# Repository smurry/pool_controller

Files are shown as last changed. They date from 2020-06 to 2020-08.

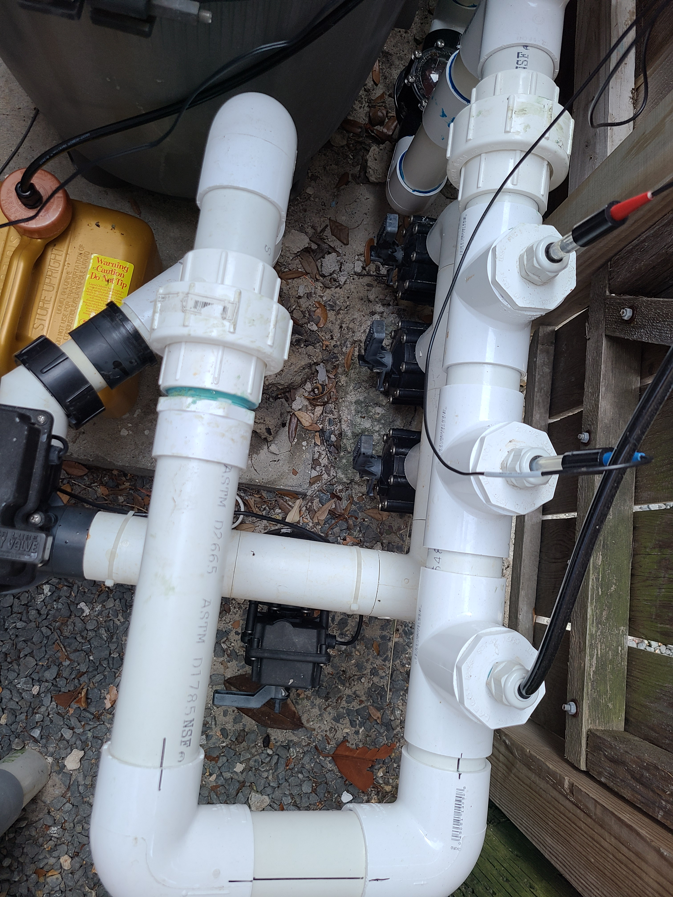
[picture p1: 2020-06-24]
Resources/Sensors and Bleach Canister.jpg

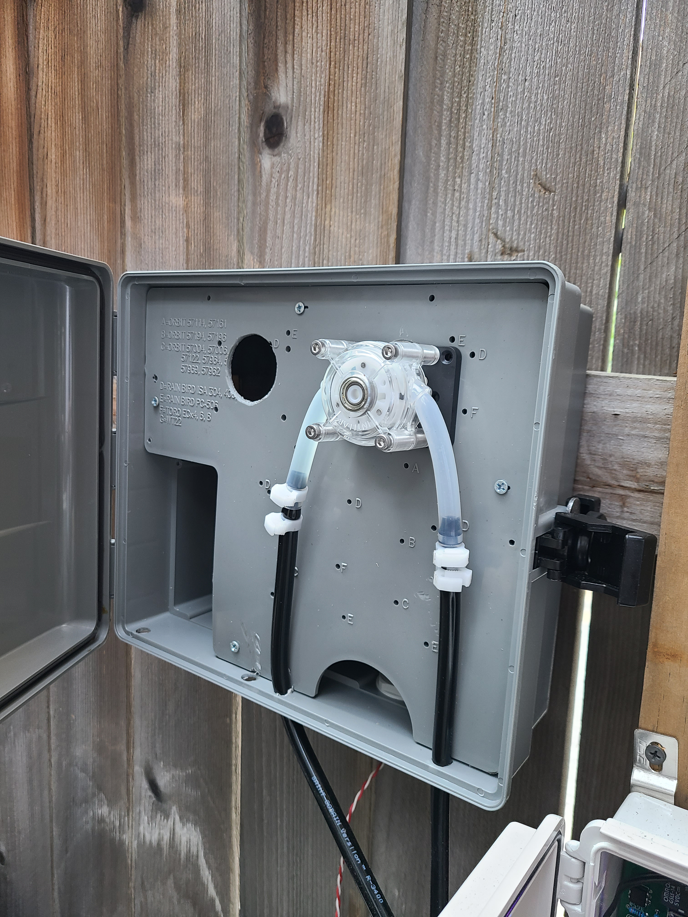
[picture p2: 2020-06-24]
Resources/Bleach Pump.jpg

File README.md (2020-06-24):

# Pool Controller
PH and ORP monitor/control for ESP32

To use, you'll need to flash an ESP32 module with micropython.  See: https://micropython.org/download/esp32/.  Version must be May 20,2020 or later.

You must update the conf-example.sample file:
  1)  edit wifi information and mqtt server information as noted in the file.  All values need to be in quotation marks as in the example file.
  2)  save the file with exactly this filename: conf.txt

After saving the conf.txt file, upload conf.txt, config.py, mqtt_as.py and main.py to the ESP32.  If you are unfamiliar with how to do this, check out https://github.com/BetaRavener/uPyLoader

The sensors configured in the conf.txt file represent IO ports on the ESP32-DEVKITC board.  They are designed to work with isolated carrier boards from Atlas Scientific (for example https://www.atlas-scientific.com/carrier-boards/electrically-isolated-ezo-carrier-board-gen-2/).  You will need to purchase the carrier boards, EZO modules, and probes from Atlas.

Outputs are provided on the IO ports noted in the conf.txt file for Ph Pump (i.e. acid) and ORP Pump (i.e. bleach).  These pins can be connected through appropriate isolation and relays to peristaltic pumps used to dispense the required chemicals into the pool.

This system was designed to work with Home Assistant, although in principle any MQTT-enabled controller should work.  Configuration files for Home Assistant are in the directory "Home Assistant."  The .yaml package goes into your packages directory and the pool_fc.py is an appdaemon file and should go in the appropriate appdaemon folder.

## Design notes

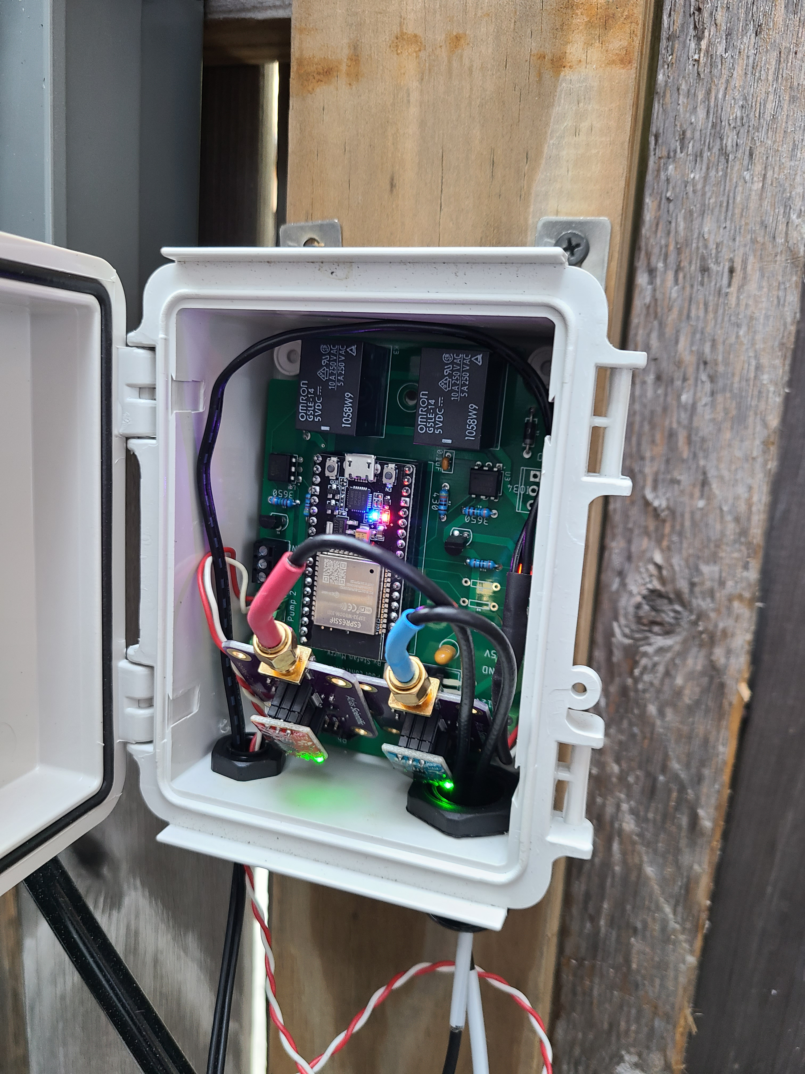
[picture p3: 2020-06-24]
Resources/PH-ORP Controller v2.jpg

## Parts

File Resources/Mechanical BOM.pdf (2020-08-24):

Other parts you’ll need:

Qty | Description | P/N | Website | Notes
6 | Cable Glands | RDC16NA‐GR | https://www.elecdirect.com/cord‐grips‐strain‐relief/cable‐glands/dome‐cap‐cable‐gland‐1‐2‐npt‐39‐ 56‐gray‐complete‐with‐o‐ring‐locknut
2 | Peristaltic Pumps | DP520‐460 | https://www.aliexpress.com/item/32972643254.html?spm=a2g0s.9042311.0.0.55f94c4dxG6wrN
1 | 12VDC Power Supply | N/A | https://www.amazon.com/gp/product/B07H23JGS6/ref=ppx_yo_dt_b_asin_title_o03_s00?ie=UTF8&psc=1
Vari es | 1/4" ID x 3/8" OD x 1/16" Wall Versilon™ R‐3400 UV Resistant Tubing | 33932 | https://www.usplastic.com/catalog/item.aspx?itemid=3 3932 | Sold in 10’ lengths. Need to order as much as needed for your project
4 | .351" Min. to .394" Max. Snap Grip Clamp | 34082 | https://www.usplastic.com/catalog/item.aspx?itemid=3 4082
2 | 1/4" Hose ID x 1/4" Hose ID Black HDPE Connector | 28098 | https://www.usplastic.com/catalog/item.aspx?itemid=2 8098
1 | Outdoor Timer Box | 57095 | https://www.homedepot.com/p/Orbit‐Outdoor‐Timer‐Box‐57095/100158884
1 | Control Board Box | WH‐02 | https://www.polycase.com/wh‐02 | Box matches the board outline and mounting holes

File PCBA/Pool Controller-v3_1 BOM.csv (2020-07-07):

Qty | Value | Device | Package | Parts | Digikey P/N | Price (USD) | Line (USD)
4 |  | Screw Terminal Connector - 2 places | SCREWTERMINAL-3.5MM-2 | J1, J3, J4, J11 | 609-4725-ND | 0.69 | 2.76
2 |  | Screw Terminal Connector - 3 places | SCREWTERMINAL-3.5MM-3 | J6, J12 | ED2741-ND | 0.42 | 0.84
2 |  | Screw Terminal Connector - 4 places | SCREWTERMINAL-3.5MM-4 | J13 | use 2 609-4725-ND | 0.69 | 1.38
1 |  | Switching Regulator-5.5V-TPSM84205EAB | 78XXL | U4 | 296-47074-ND | 5.43 | 5.43
4 | 280 | Axial Resistor-280 ohm | AXIAL-0.3 | R7, R8, R9, R10 | 280XBK-ND | 0.04 | 0.16
1 | 0.1uF | Radial Capacitor - 0.1 uF | CAP-PTH-SMALL-KIT | C1 | 399-9859-1-ND | 0.16 | 0.16
2 | 47uF | Radial Ceramic Capacitor - 47 uF | CPOL-RADIAL-2.5MM-5MM-KIT | C2, C3 | 445-173152-1-ND | 1.09 | 2.18
1 | 10uF | Radial Capacitor - 10 uF | CPOL-RADIAL-2.5MM-5MM-KIT | C4 | 399-3565-ND | 1.50 | 1.50
2 | 1A/50V/1.1V | Radial Diode-1N4001 | DIODE-1N4001 | D1, D2 | 641-1310-1-ND | 0.09 | 0.17
2 | 200mA/40V | NPN Transistor -2N3904 | TO-92 | Q1, Q3 | 2N3904FS-ND | 0.16 | 0.32
2 | 3650 | Axial Resistor-3650 ohm | AXIAL-0.3 | R3, R4 | 3.65KXBK-ND | 0.06 | 0.11
2 | 430 | Axial Resistor-430 ohm | AXIAL-0.3 | R1, R2 | 432XBK-ND | 0.06 | 0.11
1 | 4700 | Axial Resistor-4700 ohm | AXIAL-0.3 | R5 | 4.75KXBK-ND | 0.06 | 0.06
2 | CNY17-1 | Optoisolator - CNY17-1 | DIP762W50P254L730H410Q6 | U2, U3 | 160-1308-5-ND | 0.38 | 0.75
1 | ESP32-DEVKITC-32D | ESP32-DEVKITC-32D | MODULE_ESP32-DEVKITC-32D | U1 | 1965-ESP32-DEVKITC-32UE-ND | 10.00 | 10.00
2 | RELAY-SPDT | Relay - SPDT | RELAY_G5LE | K2, K3 | Z1011-ND | 1.35 | 2.70
2 |  | 5 position header |  | J2, J5 | S6103-ND | 0.47 | 0.94
1 | 623nm | Red LED |  | J10 | 160-1087-ND | 0.36 | 0.36
 |  |  |  |  |  |  | 29.94

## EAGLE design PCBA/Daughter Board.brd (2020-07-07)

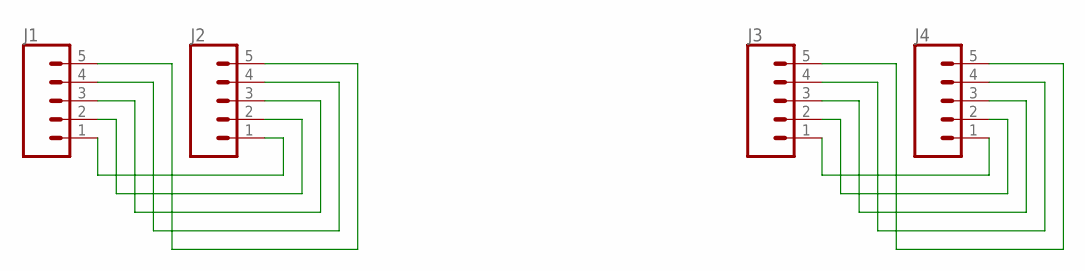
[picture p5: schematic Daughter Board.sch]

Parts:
J1, J2, J3, J4: CONN_05; 1X05

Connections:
unnamed: J1.1, J2.1
unnamed: J1.2, J2.2
unnamed: J1.3, J2.3
unnamed: J1.4, J2.4
unnamed: J1.5, J2.5
unnamed: J3.1, J4.1
unnamed: J3.2, J4.2
unnamed: J3.3, J4.3
unnamed: J3.4, J4.4
unnamed: J3.5, J4.5

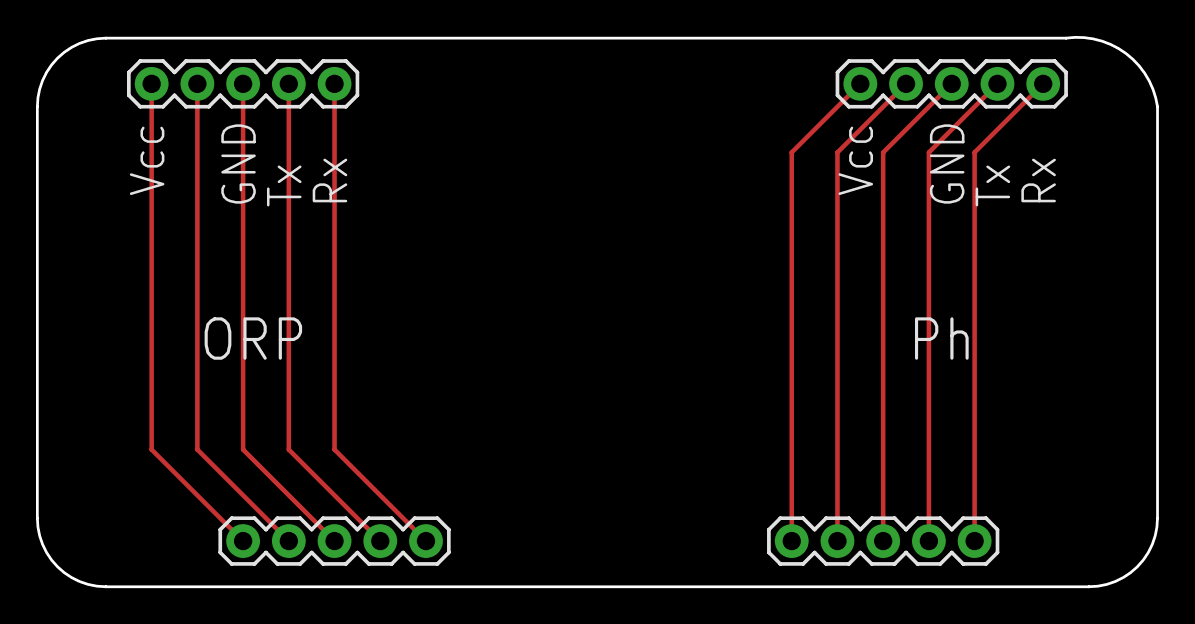
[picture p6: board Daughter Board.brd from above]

Board: 2 copper layers, 62.2 x 30.5 mm, 4 parts (0 on the bottom side), 10 nets.

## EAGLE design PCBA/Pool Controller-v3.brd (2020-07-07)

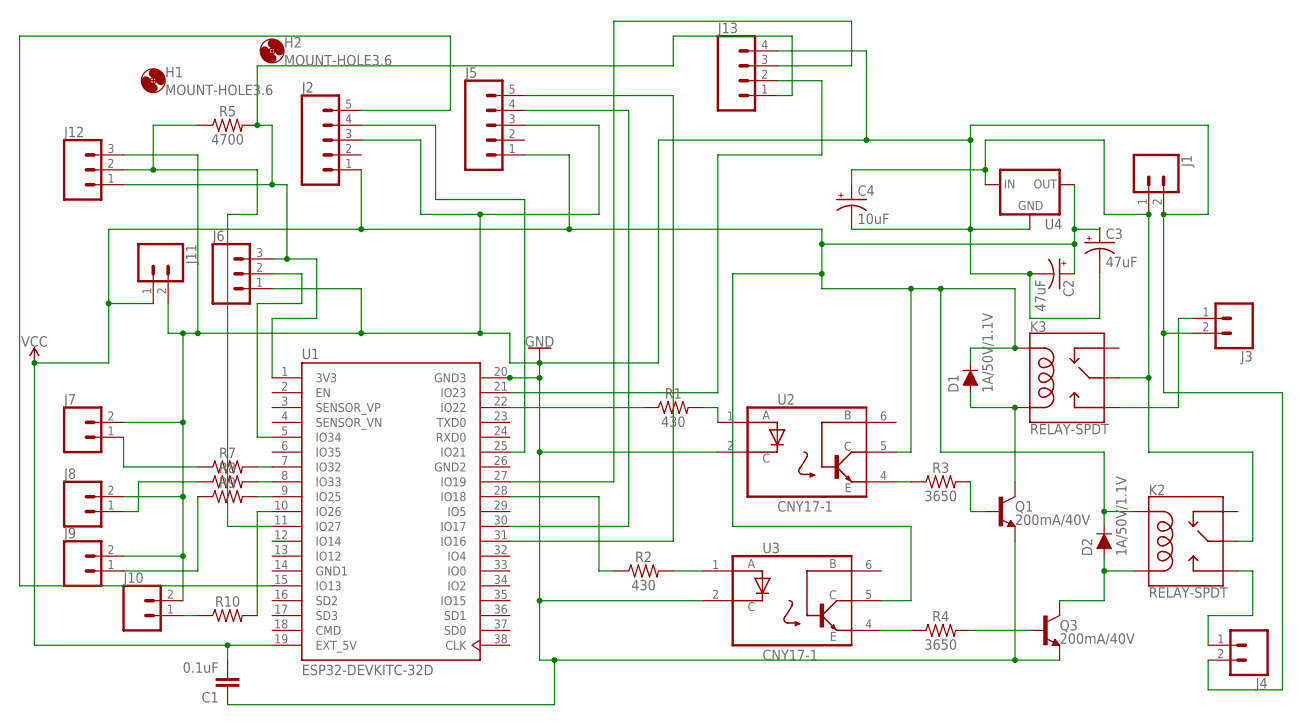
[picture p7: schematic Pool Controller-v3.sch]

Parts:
C1: 0.1uF; CAP-PTH-SMALL-KIT
C2: 47uF; CPOL-RADIAL-2.5MM-5MM-KIT
C3: 47uF; CPOL-RADIAL-2.5MM-5MM
C4: 10uF; CPOL-RADIAL-2.5MM-5MM
D1, D2: 1A/50V/1.1V; DIODE-1N4001
H1, H2: MOUNT-HOLE3.6; 3,6
J1, J3, J4, J11: CONN_023.5MM; SCREWTERMINAL-3.5MM-2
J2, J5: CONN_05; 1X05
J6, J12: CONN_03SCREW; SCREWTERMINAL-3.5MM-3
J7, J8, J9, J10: CONN_02; 1X02
J13: CONN_04SCREW; SCREWTERMINAL-3.5MM-4
K2, K3: RELAY-SPDT; RELAY_G5LE
Q1, Q3: 200mA/40V; TO-92
R1, R2: 430; AXIAL-0.3
R3, R4: 3650; AXIAL-0.3
R5: 4700; AXIAL-0.3
R7, R8, R9, R10: AXIAL-0.3
U1: ESP32-DEVKITC-32D; MODULE_ESP32-DEVKITC-32D
U2, U3: CNY17-1; DIP762W50P254L730H410Q6
U4: V_REG_78XXSIDE; 78XXL

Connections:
GND: C1.1, C2.2 (-), C3.2 (-), C4.2 (-), J1.2, J2.3, J3.2, J4.2, J5.3, J6.1, J7.2, J8.2, J9.2, J10.2, J11.2, J12.3, J13.4, Q1.1 (E), Q3.1 (E), U1.20 (GND3), U2.2 (C), U3.2 (C), U4.GND
GND1: U1.14 (GND1)
GND2: U1.26 (GND2)
unnamed: R2.P$2 (2), U3.1 (A)
unnamed: R1.P$1 (1), U1.22 (IO22)
unnamed: R1.P$2 (2), U2.1 (A)
unnamed: R2.P$1 (1), U1.28 (IO18)
unnamed: R3.P$1 (1), U2.4 (E)
unnamed: Q1.2 (B), R3.P$2 (2)
unnamed: D1.A, K3.5 (COIL2), Q1.3 (C)
unnamed: C4.1 (+), J1.1, K2.1 (MAIN), K3.1 (MAIN), U4.IN
unnamed: J5.4, U1.30 (IO17)
unnamed: J3.1, K3.3 (NO)
unnamed: J6.3, J12.1, J13.1, R5.P$2 (2), U1.1 (3V3)
unnamed: D2.A, K2.5 (COIL2), Q3.3 (C)
unnamed: J4.1, K2.3 (NO)
unnamed: R4.P$1 (1), U3.4 (E)
unnamed: Q3.2 (B), R4.P$2 (2)
unnamed: J6.2, U1.5 (IO34)
unnamed: J2.5, U1.15 (IO13)
unnamed: J2.4, U1.25 (IO21)
unnamed: J5.5, U1.31 (IO16)
unnamed: J12.2, R5.P$1 (1), U1.11 (IO27)
unnamed: R7.P$2 (2), U1.7 (IO32)
unnamed: J7.1, R7.P$1 (1)
unnamed: R8.P$2 (2), U1.8 (IO33)
unnamed: J8.1, R8.P$1 (1)
unnamed: R9.P$2 (2), U1.9 (IO25)
unnamed: J9.1, R9.P$1 (1)
unnamed: J10.1, R10.P$1 (1)
unnamed: R10.P$2 (2), U1.10 (IO26)
unnamed: J13.3, U1.27 (IO19)
unnamed: J13.2, U1.21 (IO23)
VCC: C1.2, C2.1 (+), C3.1 (+), D1.C, D2.C, J2.1, J5.1, J11.1, K2.2 (COIL1), K3.2 (COIL1), U1.19 (EXT_5V), U2.5 (C`), U3.5 (C`), U4.OUT

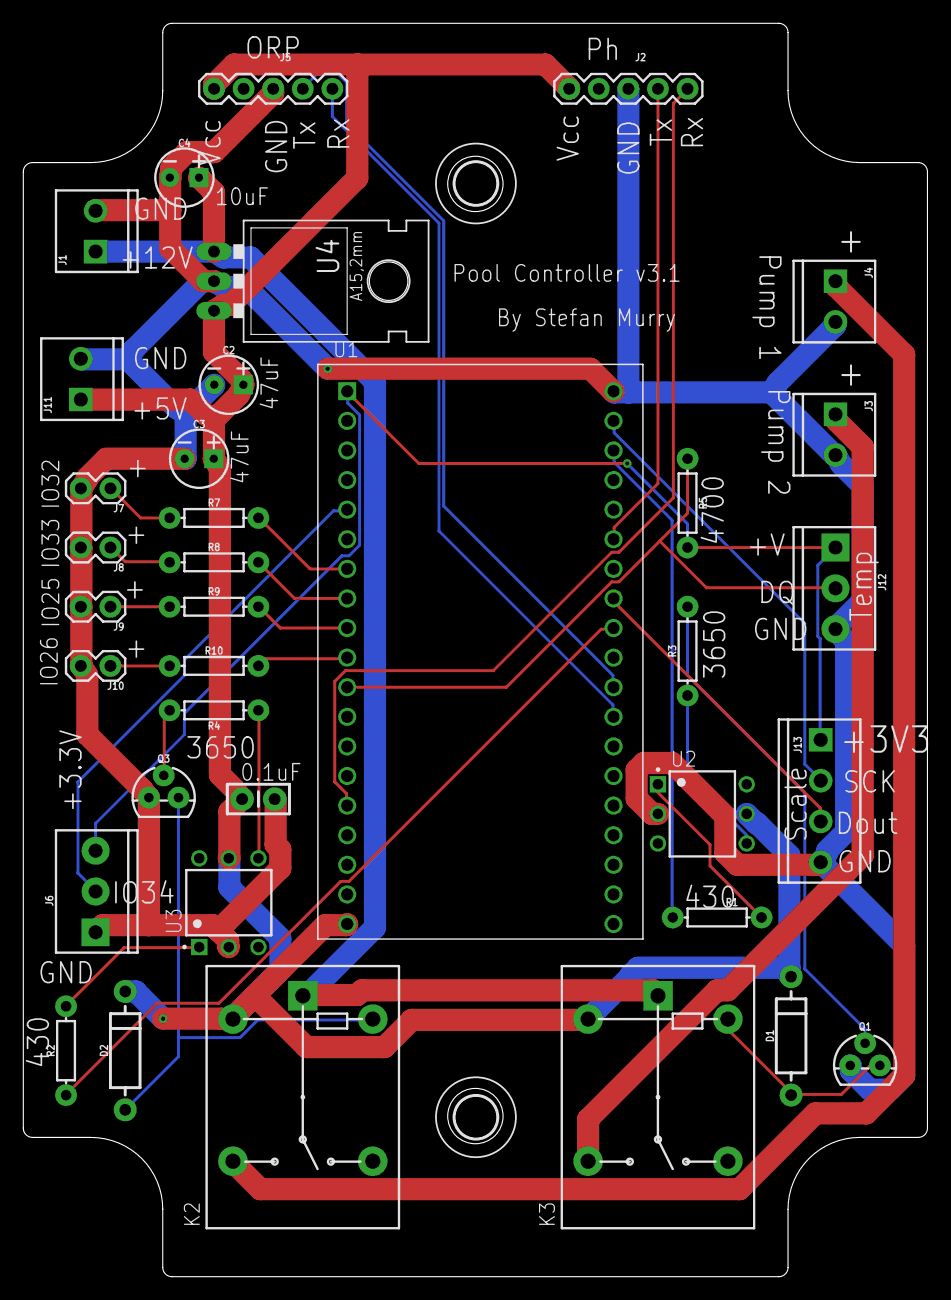
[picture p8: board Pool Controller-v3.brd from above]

Board: 2 copper layers, 77.6 x 107.6 mm, 38 parts (0 on the bottom side), 32 nets.

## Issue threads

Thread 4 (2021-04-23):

Free Chlorine stopped working

kgalilio, 2021-04-23:
Hi,
Thanks for the highly detailed guidance.
I have been using the pool_fc.py app in AppDaemon without any issues. Recently I have updated my hassio and AppDaemon to the latest releases, and for some reason I stopped getting the FC readings!
Not sure if it has anything to do with the upgrades, but those are about the only changes I've made recently.

The Error log in AppDaemon shows the following:
`2021-04-24 00:03:19.031463 WARNING free_chlorine: ------------------------------------------------------------
2021-04-24 00:03:19.031384 WARNING free_chlorine: Worker Ags: {'id': '808d559799674797b7b88deea12a8df5', 'name': 'free_chlorine', 'objectid': '572efedf5c354bd9a20f99ec18ac0fe3', 'type': 'state', 'function': >, 'attribute': 'state', 'entity': 'sensor.swimming_pool_ph', 'new_state': '11.77', 'old_state': '11.71', 'pin_app': True, 'pin_thread': 0, 'kwargs': {'__thread_id': 'thread-0'}}
2021-04-24 00:03:19.031280 WARNING free_chlorine: Unexpected error in worker for App free_chlorine:
2021-04-24 00:03:19.031169 WARNING free_chlorine: ------------------------------------------------------------
2021-04-24 00:02:26.272568 WARNING free_chlorine: ------------------------------------------------------------
2021-04-24 00:02:26.272460 WARNING free_chlorine: Traceback (most recent call last):
  File "/usr/lib/python3.8/site-packages/appdaemon/threading.py", line 903, in worker
    funcref(
  File "/config/appdaemon/apps/pool_fc.py", line 33, in calc_fc
    for k,v in ch[last_orp].items():
KeyError: 0`

I have copied your pool_fc.py as is, therefore this is what I have at line 33:
`for k,v in ch[last_orp].items():`

I am wondering if anyone else is having the same problem, and if anyone has figured out how to fix it.
Any help would be greatly appreciated.

smurry, 2021-04-23:
Thanks for sending the detailed troubleshooting data.  I haven’t seen this error before, however from the description I would say that it may be that your sensor.pool_orp is reading zero (0).  Can you check the state of this sensor and make sure it is reading something sensible?

--Stefan

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

kgalilio, 2021-04-30:
For some reason my ORP sensor went crazy! I had to re-calibrate it again and all is fixed.
Thanks for your help.

kgalilio, 2021-04-30:
Works like a charm.

Closed 2021-04-30.

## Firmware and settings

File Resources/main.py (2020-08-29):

"""
Currently in git version control v0.1 branch.

Zone Controller for irrigation system.  Designed to be run on an ESP32 controller.

Listens for incoming MQTT commands, formatted as follows:

    {command}:zone:time

for example: 'water:1:5' would open the zone 1 vale for 5 minutes.
similarly, 'water:2:10' would open the zone 2 valve for 10 minutes.

Basic program flow:

Create a class called zone, which has attributes zone_id, active and methods like turn_on and turn_off

"""

import machine
from machine import Pin, RTC
import time
from robust import MQTTClient
import json
import ubinascii

# Load configuration from file
with open (r'conf.txt', 'rt') as File_object:     # Open conf.txt for reading text
    config = File_object.read()                   # Read the entire file into a variable

d = json.loads(config)

#print(d)

mqtt_server = d['mqtt_server']
topic_sub = d['topic_sub'].encode('utf-8')
topic_pub = d['topic_pub'].encode('utf-8')
zones = d['zones']
keepalive_interval = int(d['keepalive_interval'])
mqtt_pw = d['mqtt_pw']
mqtt_username = d['mqtt_username']

print('server: {},Sub topic: {}, Pub Topic: {}'.format(mqtt_server, topic_sub, topic_pub))
zone_count = len(d['zones'])

#print('zones: {}'.format(zones))

# create a command stack.  This stack will be a list of lists containing the commands received and their arguments
# for example, [[water:1:5]] would be a command to water zone 1 for 5 minutes.
c_stack = []
stop_now = False
lastping = 0
#print('just before rtc')
#rtc = RTC()
d=RTC().datetime()
res = "{}-{:02}-{:02} {}:{}:{}".format(str(d[0])[2:], d[1], d[2], d[4], d[5], d[6])
#print('Just got RTC at: %s' %res)

client_id = ubinascii.hexlify(machine.unique_id())

def exit_handler():
    print("Application Ending.")
    pub("Disconnecting")
    client.disconnect()
    raise

def get_last_cmd(ls):
  if ls != []:
    c = ls[len(ls)-1][0]
    return c
  return []

def format_now():
  d=RTC().datetime()
  res = "{}-{:02}-{:02} {:02}:{:02}:{:02}".format(str(d[0])[2:], d[1], d[2], d[4], d[5], d[6])
  return(res)

def pull_cmd(ls):
    ls.reverse()
    elem = ls.pop()
    ls.reverse()
    a = elem[0]
    b = int(elem[1])
    c = int(elem[2])
    return a,b,c


def sub_cb(topic, msg):
  # whenever there is a new message posted, check the topic.  If it is a command to the controller, then check if it is a stop command.
  # Flag a stop command to be dealt with immediately.  Otherwise, throw the command onto the stack.
  global c_stack, stop_now, topic_sub
  #print((topic, msg))
  if topic == topic_sub:
    #print('Received command: %s' %msg)
    new_string=str(msg, 'utf-8')
    #print('Received command: %s' %new_string)
    new_msg = new_string.split(':')
    #print(new_msg)
    # TODO: move this next part to its own method.  Something like check_special to look for commands that need
    # to be processed immediately (not added to the back of the queue).  Add a "status" special command to get
    # current zone status.
    if new_msg[0] == 'stop':
        stop_now = True
        return
    else: c_stack.append(new_msg)
    #print(c_stack)
    return

def pub(msg):
  global client_id, mqtt_server, topic_pub
  client.publish(topic_pub, msg.encode('utf-8'))

def connect_and_subscribe():
  global client_id, mqtt_server, topic_sub, mqtt_pw, mqtt_username
  client = MQTTClient(client_id, mqtt_server, 0, mqtt_username, mqtt_pw, keepalive_interval, False, {})
  print('About to try to connect to %s MQTT broker, subscribed to %s password %s username' % (mqtt_server, mqtt_pw, mqtt_username))
  client.DEBUG = True
  client.set_callback(sub_cb)
  if not client.connect(clean_session=False):
    print("New session being set up")
    client.subscribe(topic_sub)
  else:
    print('do not set up new session, reconnect to existing one...')
    client.subscribe(topic_sub)
  print('Connected to %s MQTT broker, subscribed to %s topic' % (mqtt_server, topic_sub))
  return client

def restart_and_reconnect():
  print('Failed to connect to MQTT broker. Reconnecting...')
  time.sleep(5)
  machine.reset()

def is_connected():
  station = network.WLAN(network.STA_IF)
  #print('IP Address: %s' %station.ifconfig()[0])
  b=station.ifconfig()[0][0]
  #print(b)
  if b == '0': return False
  else: return True

def keepalive_check(tm):
    now = time.time()
    if (now - tm) > keepalive_interval:
        client.ping()
        print('Sent ping at {}'.format(now))
        return now
    else: return tm

class Zone:

    def __init__(self,zone_id,st,active = True):
        """

        :param zone_id: zone ID (number)
        :param active: Boolean, whether zone is active or not
        :param st: Boolean, zone is currently on/off
        """
        self.zone_id=zone_id
        self.active=active
        self.st=st

    def turn_on(self):
        if self.active:
            valve[self.zone_id].on()
            print('valve {} on'.format(self.zone_id))
            self.st=True
        else:
            print('zone not active.  cannot turn on')

    def turn_off(self):
        if self.active:
            valve[self.zone_id].off()
            print('valve {} off'.format(self.zone_id))
            self.st=False
        else:
            print('zone not active.  cannot turn off.')


#class Controller:
#    def __init__(self):
        """
        :param stack: Command stack
        """
#        self.stack=stack

#print('entering main')
try:
 now_dt = format_now()
 print('Successful Boot at: %s' %now_dt)
 client = connect_and_subscribe()
 pub(now_dt)

except OSError as e:
  print("OS error: {0}".format(e))
  restart_and_reconnect()


#instantiate a controller and zones

valve = []
#c = Controller()
valve.insert(0, Pin(2, Pin.OUT))
blue_led = valve[0]
for i in range(1, (zone_count+1)):
    valve.insert(i, Pin(int(zones['zone{}'.format(i)]),Pin.OUT))

for i in range(zone_count+1):
    print('valve{}: {}'.format(i,valve[i]))


#instantiate zones:
zone = []
zone.insert(0, Zone(0,False,True))
for i in range(1, zone_count+1):
    zone.insert(i, Zone(i,False,True))
    #print('zone: {}'.format(zone[i]))

watering = False

while True:
    try:
        # check for incoming MQTT message. If the last message received is a stop command, then shut stuff off
        # check if there is a connection to the MQTT server.  If so, check for a message
        is_message = client.check_msg()
        # if is_message is "Error" then we are not connected to the MQTT server.  First, check whether the internet is connected
        # if internet is connected, then try to reconnect to the MQTT server.
        if is_message == 'Error':
          print('is_message: {}'.format(is_message))
          print('Error connecting to MQTT server.  Attempting reconnect')
          print('Connection Status: {}'.format(is_connected()))
          if is_connected():
              client.reconnect()
              lastping = time.time()
          else: pass
        lastping = keepalive_check(lastping)

       # at this point, there is no internet connection, so keep running the try loop here to see if the timer has expired and the
       # water needs to be shut off.  Then loop again and see if the internet and MQTT servers can be reconnected

        #print('MQTT: %s' %is_message)
        #print('Type: %s' %type(is_message))

        time.sleep(1)
        # check for incoming MQTT message. If the last message received is a stop command, then shut stuff off
        if stop_now:
          print('Shutting down all zones.')
          mes = ''
          for i in range(0, zone_count+1):
              zone[i].turn_off()
              mes = mes + 'zone{}:{}'.format(i,zone[i].st) + ','
          mes = mes.rstrip(',')
          print(mes)
          pub(mes)
          watering = False
          #if everything is stopped, clear the command stack
          c_stack = []
          now_dt = format_now()
          stop_now = False

          # if already watering, then skip opening valves, otherwise if there's a command waiting, start watering
        if (c_stack != [] and (not watering)):
            c_stack.reverse()
            comm=c_stack.pop()
            c_stack.reverse()
            if comm[0] == 'water':
                zone[int(comm[1])].turn_on()
                start_time=time.time()
                watering = True

            t=float(comm[2])
            d=RTC().datetime()
            res = "{}-{}-{} {}:{}:{}".format(str(d[0])[2:], d[1], d[2], d[4], d[5], d[6])
            print('opening valve%s for %f minutes, starting at %s' %(comm[1], t, res))
            mes = ''
            for i in range(0, zone_count+1):
                    mes = mes + 'zone{}:{}'.format(i,zone[i].st) + ','
            mes = mes.rstrip(',')
            print(mes)
            pub(mes)

        if watering:
            if ((time.time()-start_time) >= (t*60)):
                mes = ''
                print('time up.  Stopping water at: %f' %time.time())
                watering = False
                for i in range(0, zone_count+1):
                    zone[i].turn_off()
                    mes = mes + 'zone{}:{}'.format(i,zone[i].st) + ','
                mes = mes.rstrip(',')
                print(mes)
                pub(mes)

    except OSError as e:
        print("OS error: {0}".format(e))
        #client.disconnect()
        restart_and_reconnect()

    except KeyboardInterrupt as e:
        exit_handler()

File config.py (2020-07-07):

# config.py Local configuration for pool controller v3
from sys import platform
from mqtt_as import config
import json
import ubinascii
import machine, onewire, ds18x20
import scales


# Load configuration from file
with open (r'conf.txt', 'rt') as File_object:     # Open conf.txt for reading text
    conf = File_object.read()                   # Read the entire file into a variable

d = json.loads(conf)

# Set up config variables
topic_sub = d['topic_sub'].encode('utf-8')
ph_topic_pub = d['ph_topic_pub'].encode('utf-8')
orp_topic_pub = d['orp_topic_pub'].encode('utf-8')
resp_pub = d['resp_pub'].encode('utf-8')
report_interval = int(d['report_interval'])

config['server'] = d['mqtt_server']  # MQTT Broker Address
config['port'] = int(d['mqtt_port']) #MQTT Broker Port
config['user'] = d['mqtt_username'] # MQTT Broker Username
config['password'] = d['mqtt_pw'] #MQTT Broker Password
config['ssid'] = d['ssid'] #WiFi SSID
config['wifi_pw'] = d['password'] # Wifi Password
config['keepalive'] = int(d['keepalive_interval'])
config['hostname'] = d['hostname'] # configure human-readable Wifi hostname

class Sensor:
    with open (r'conf.txt', 'rt') as File_object:     # Open conf.txt for reading text
        conf = File_object.read()                   # Read the entire file into a variable

    global d
    d = json.loads(conf)

    ph_uart_port=int(d['ph_uart_port']) # UART port on the ESP32 used for the PH sensor
    ph_tx = int(d['ph_tx']) # PH sensor Tx pin
    ph_rx = int(d['ph_rx']) # PH sensor Rx pin
    orp_uart_port=int(d['orp_uart_port']) # UART port on the ESP32 used for the ORP sensor
    orp_tx = int(d['orp_tx']) # ORP sensor Tx pin
    orp_rx = int(d['orp_rx']) # ORP sensor Rx pin
    repl_button = machine.Pin(0, machine.Pin.IN, machine.Pin.PULL_UP) #define a button which will exit the program
    report_interval = int(d['report_interval']) # how often are Ph and ORP values sent over MQTT (sec)
    ph_ma_window = int(d['ph_ma_window']) # how many datapoints in the moving average window
    orp_ma_window = int(d['orp_ma_window'])
    load_cell_d_out_pin = int(d['load_cell_d_out_pin'])
    load_cell_pd_sck_pin = int(d['load_cell_pd_sck_pin'])

class Pump:
    global d
    pump_1_pin=machine.Pin(int(d['pump_1_pin']), machine.Pin.OUT)
    pump_2_pin=machine.Pin(int(d['pump_2_pin']), machine.Pin.OUT)
    PH_PUMP = int(d['ph_pump'])
    ORP_PUMP = int(d['orp_pump'])

class Temp_sensor():
    global d
    def __init__(self):
        self.ds_pin = machine.Pin(int(d['ds_pin']))
        self.ds_sensor = ds18x20.DS18X20(onewire.OneWire(self.ds_pin))

    def scan(self):
        roms=self.ds_sensor.scan()
        print('Found DS devices: {}'.format(roms))
        return roms

    def convert_temp(self):
        c=self.ds_sensor.convert_temp()
        print(c)
        return c

    def read_temp(self, rom):
        c = self.ds_sensor.read_temp(rom)
        print(c)
        return c




# I haven't tested with platforms other than ESP32, but the following pin definitions for the LEDs
# are known to vary across the different platforms.

if platform == 'esp8266' or platform == 'esp32' or platform == 'esp32_LoBo':
    from machine import Pin
    def ledfunc(pin):
        pin = pin
        def func(v):
            pin(not v)  # Active low on ESP8266
        return func
    wifi_led = ledfunc(Pin(26, Pin.OUT, value = 0))  # Red LED for connected to broker
    blue_led = ledfunc(Pin(2, Pin.OUT, value = 1))  # WiFi connected or message received
elif platform == 'pyboard':
    from pyb import LED
    def ledfunc(led, init):
        led = led
        led.on() if init else led.off()
        def func(v):
            led.on() if v else led.off()
        return func
    wifi_led = ledfunc(LED(1), 1)
    blue_led = ledfunc(LED(3), 0)

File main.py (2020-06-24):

# Pool Controller v3 by Stefan Murry
# main.py
# (C) Copyright Stefan Murry 2020.
# Released under the MIT licence.

# Public brokers https://github.com/smurry/Pool_controller

# This code was written for the ESP32 DEVC from expressif.  Various other versions of this module
# have been tested as well.

# the code below uses asyncio which requires a recent (more recent than May 20, 2020) micropython firmware for the ESP32
# firmware can be downloaded from here: https://micropython.org/download/esp32/

from mqtt_as import MQTTClient, config
from config import wifi_led, blue_led, ph_topic_pub, orp_topic_pub, topic_sub, resp_pub, Sensor, Pump, Temp_sensor
import uasyncio as asyncio
from machine import Pin, RTC, UART, reset
from array import *
import time
import sys
import network

loop = asyncio.get_event_loop()
outages = 0
ph_vals=[] # list to hold ph values
orp_vals=[] # list to hold ORP values
cal_finish=False

# pushing the right button on the ESP32 will exit the program back to REPL
def exit_to_repl(pin):
    client.close()
    blue_led(True)
    sys.exit('Exiting to REPL')

# RSSI is available if your WiFi is broadcasting an SSID.  Doesn't work if
# the SSID is not broadcast.
async def get_rssi():
    global rssi
    s = network.WLAN()
    ssid = config['ssid'].encode('UTF8')
    try:
        rssi = [x[3] for x in s.scan() if x[0] == ssid][0]
    except IndexError:  # ssid not found.
        rssi = -199
    print('RSSI: {}'.format(rssi))
    loop.create_task(client.publish(resp_pub, 'RSSI: {}'.format(rssi), qos = 1))

# Temperature is read from a DS18B20 Temperature sensor.  In principle, many sensors
# can be connected if desired.
async def get_temp():
    try:
        t=Temp_sensor()
        roms=t.scan()
        t.convert_temp()
        await asyncio.sleep(0.75)
        for rom in roms:
            temp=t.read_temp(rom)
            print('rom: {}'.format(rom))
            print('temp: {}'.format(temp))
            loop.create_task(client.publish(resp_pub, 'temp: {}'.format(temp), qos = 1))
    except:
        loop.create_task(client.publish(resp_pub, 'temp sensor error', qos = 1))

async def send_command(u, cmd):
    command_to_send=cmd+'\r'
    resp=u.write(command_to_send)
    print('Received response: {}'.format(resp))
    return resp

# in addition to providing the latest pH and ORP values, the program will provide
# a moving average value.  Averaging window is defined in the config.txt file
def moving_average(a, v, w): # an existing list of values, a new value, and an averaging window
    a.append(v) # add new value to the list
    if len(a)>w:
        a.pop(0) # if the new list is longer than the window, then pop the oldest item
    avg=sum(a)/len(a) # average the new list
    return(a, avg)

async def read_response(u):
    try:
        r=u.read().decode("utf-8")
        print('response: {}'.format(r))
    except:
        print('{} timeout'.format(u))
        r='8.888' + '\r' # in case of a timeout, send a default 8.888 pH value
    return r


async def read_ph(u):
     await send_command(u, 'R')
     await asyncio.sleep(1)
     reading = await read_response(u)
     ph=float(reading.split('\r')[0])
     return ph

async def read_orp(u):
     await send_command(u, 'R')
     await asyncio.sleep(1)
     reading = await read_response(u)
     orp=float(reading.split('\r')[0])
     return orp


async def pulse():  # This demo pulses blue LED each time a subscribed msg arrives.
    blue_led(True)
    await asyncio.sleep(0.5)
    blue_led(False)
    await asyncio.sleep(0.5)
    return True

async def turn_on_pump(pump, on_time):
    if pump == Pump.PH_PUMP:
        print('turning on pump {}'.format(pump))
        Pump.pump_1_pin.on()
        asyncio.create_task(client.publish(resp_pub, 'ph:on', qos = 1))
        w = await (asyncio.sleep(on_time))
        print('turning off pump {}'.format(pump))
        Pump.pump_1_pin.off()
        asyncio.create_task(client.publish(resp_pub, 'ph:off', qos = 1))
    elif pump == Pump.ORP_PUMP:
        print('turning on pump {}'.format(pump))
        Pump.pump_2_pin.on()
        asyncio.create_task(client.publish(resp_pub, 'orp:on', qos = 1))
        w = await (asyncio.sleep(on_time))
        print('turning off pump {}'.format(pump))
        Pump.pump_2_pin.off()
        asyncio.create_task(client.publish(resp_pub, 'orp:off', qos = 1))

    return True

async def turn_off_pump(pump, nothing):
    if pump==Pump.PH_PUMP:
        print('turning off pump {}'.format(pump))
        Pump.pump_1_pin.off()
        await client.publish(resp_pub, 'ph:off', qos = 1)
    elif pump == Pump.ORP_PUMP:
        print('turning off pump {}'.format(pump))
        Pump.pump_1_pin.off()
        await client.publish(resp_pub, 'orp:off', qos = 1)
    return True

async def calibrate(sensor, interval, timeout=300):
    global cal_finish
    global ph_uart
    global orp_uart

    cal_start=time.time()
    print('cal_start: {}'.format(cal_start))
    await client.publish(resp_pub, 'cal:{}:start'.format(sensor), qos = 1)
    while True:
        if sensor==1:
            ph=await read_ph(ph_uart)
            print("Ph: {}".format(ph))
            await client.publish(ph_topic_pub, '{}'.format(ph), qos = 1)
        elif sensor==2:
            orp=await read_orp(orp_uart)
            print("ORP: {}".format(orp))
            await client.publish(orp_topic_pub, '{}'.format(orp), qos = 1)
        await asyncio.sleep(interval)
        print('time now: {}'.format(time.time()))
        if cal_finish:
            if sensor == 1:
                print('issuing Ph cal mid command')
                await send_command(ph_uart,'Cal,mid,7.00')
            elif sensor == 2:
                print('issuing ORP cal command')
                await send_command(ph_uart,'cal,225')
            print('Calibration Finished')
            await client.publish(resp_pub, 'cal:{}:end'.format(sensor), qos = 1)
            cal_finish=False
            return True
        if time.time()-cal_start > timeout:
            print('end_time: {}'.format(time.time()))
            await client.publish(resp_pub, 'cal:{}:timeout'.format(sensor), qos = 1)
            return False

async def check_cal_finish(void1,void2):
    global cal_finish
    cal_finish=True
    return True


async def unknown_command():
    print('Unknown command received, ignoring')
    return False
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

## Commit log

2020-07-07 Added PCBA Gerber and Eagle files.
    [Pool Controller-v3.brd, Pool Controller-v3.sch]
2020-07-07 Added Daughter Board
    [Daughter Board.brd, Daughter Board.sch]
2020-07-07 Added PCBA BOM
    [Pool Controller-v3_1 BOM.csv]

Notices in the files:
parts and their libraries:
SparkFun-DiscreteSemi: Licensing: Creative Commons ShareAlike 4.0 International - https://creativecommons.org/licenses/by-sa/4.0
